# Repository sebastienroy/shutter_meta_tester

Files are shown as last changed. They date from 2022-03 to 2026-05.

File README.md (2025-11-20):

# shutter_meta_tester
A project which goal is to test the accuracy of shutter speed measurement tools.  

The general idea is to produce a well controlled shutter-like device.  
This device is used to produce a controlled open time, tested with a tool such as Shutter Speed Tester.  

If the measurement result of the tool is the same as the expected value, the measurement tool is accurate.  
The point is now to produce a well controlled open time. The target times are from 1s to 1/4000s.  

We consider two ways to simulate a shutter.  
1. The more theretical is to produce a "time slot" shutter. This kind of shutter consists in a source light that is lit during a controlled duration. This kind of shutter doesn't take into account the geometrical aspect of real shutter. However, it is a good mean to check the result (and its potential bias) due to the electronic circuit of the tester. The obtained results have to be taken with a "grain of salt" as the shutter testers usually come with their own light source.  
2. A simulated shutter more close to focal plane shutters (curtain shutters) consists in creating a slot that translates at a speed similar to real shutters. This can be achieved by creating a rotating wheel, with a well controlled rotation speed.

# Time Slot shutter

## Description

The faster shutter speed we want to measure is 1/4000s = 250 micro seconds.  
Because the response time of an LED is very fast (about 10 nano seconds), it is possible produce a very well controlled light pulse using a microcontroler that lights on and off an LED. The pulse duration precision is induced by the precision of the microcontroler that controls the LED.  

## Pros/cons

- The pros
  - Easy to build
  - Easy to control the pulse duration
  - Can differentiate a potential bias due to the electronic circuit from the bias due to geometrical consideration
- The cons
  - Does not take into account the physical phenomenos induced by a physical shutter.
  - In particular, the LED produces really sharp rising anf falling edges that are absolutely not representative of real worl shutters. Real world shutter have smooth egdges. For instance, the fastest leaf shutters take 1/200s to open and 1/200s to close. In case of focal plane shutters, even though the curtains are sharp, they are measured by a sensor wich is not a single point. In case of 3mm large sensor, the rizing edge is approximately 1/1000s and the same for the falling edge.
 
## Conclusion  
What maes the real world shutter difficult to measure is that the light signal has no sharp egdge, contrary to a LED that is simply switched on and off.  
So, **using an LED to test a shutter tester does not brings any information on the accuracy of the tester**. 

## Schema  

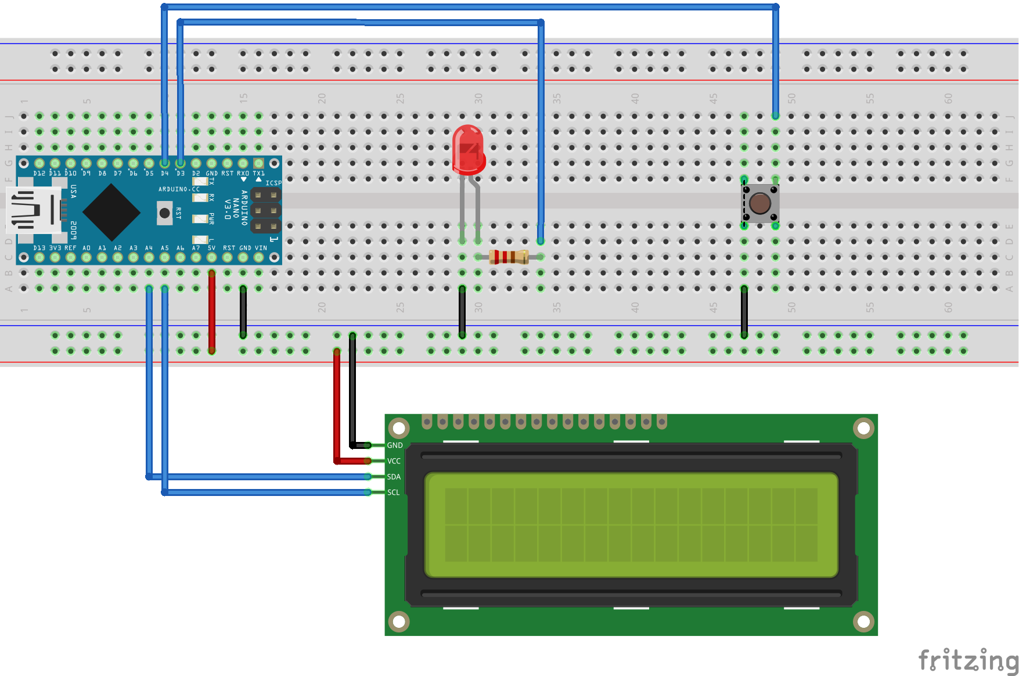
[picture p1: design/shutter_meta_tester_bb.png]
Tester schema


And the code is here :  
[Shutter Meta Tester Code](shutter_meta_tester/shutter_meta_tester.ino)

Usage :  
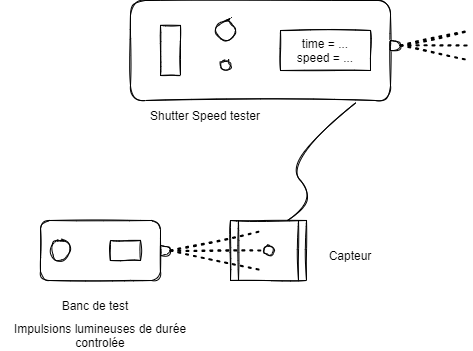
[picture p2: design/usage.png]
Usage


---

# Rotating wheel method
## Description
The idea is to use a wheel that rotates at a controlled frequency. By opening a slot in the wheel, we have the following open time :  

t = d / (2 x Pi x R x F)  

Where  
- t is the opened duration
- d is the size of the slot
- R is the radius from the wheel axis to the hole
- F is the wheel rotation frequency
 
## Pros/cons
- The pros
  - Very close to a real shutter
- The cons
  - A lot of hardware to buy
  - A lot of hardware to control 
  - A lot of parts to 3D print
 
## Conclusion
A **rotating wheel** is a lot more complicated to build than simple LED circuit, but it **is mandatory to be a little bit reprensentative of a real world shutter**.  
  
## Schema
We make the choice to control a wheel rotation using a stepper motor. The stepper motor has the advantage to be drivable very precisely, without any further regulation circuit. This stepper motor is controlled using an L298N board. This board is itself driven through the GPIO 14, 15, 16 and 17 of a Raspberry Pi Pico board.  
A push button, connected on GPIO 18, allows to start and stop the motor.  
The whole stuff is powered using a 12V DC adapter. The 5V output of the L298N bard is used to power the microcontroler board.  
The Rpi Pico has been chosen because it is cheap, available, efficient and fun : we can program it using MicroPython language (see [Rpi Pico MicroPython documentation](https://www.raspberrypi.com/documentation/microcontrollers/micropython.html))  
The microPython code used to drive all that is here. 

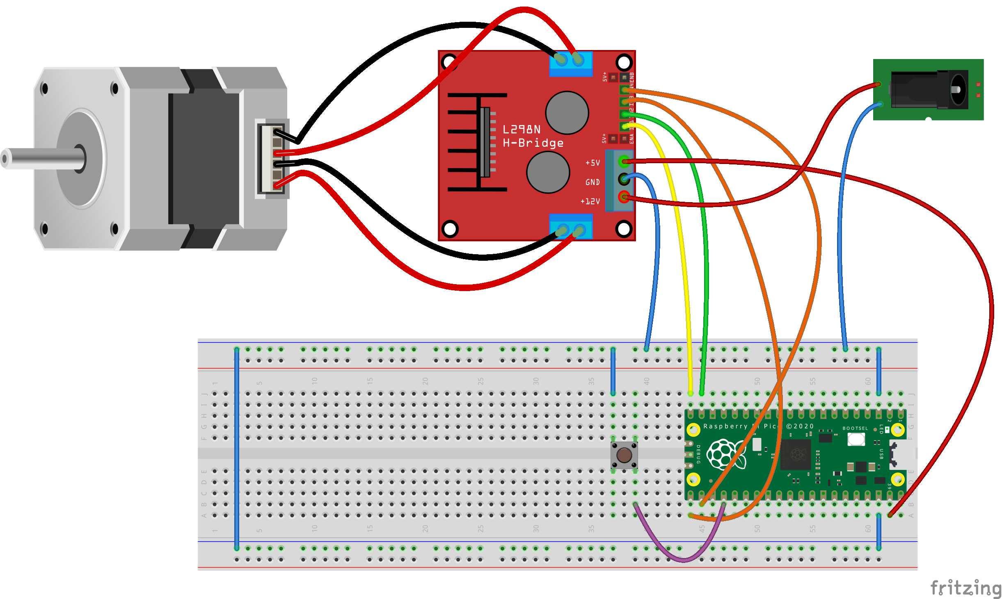
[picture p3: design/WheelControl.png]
Wheel control schema


### Bill Of Material (BOM)  

| Component | Reference|
|---|---|
| Microcontroler | https://www.kubii.fr/cartes-raspberry-pi/3205-raspberry-pi-pico-3272496311589.html#/477-version_pico-pico |
| Stepper motor | https://www.gotronic.fr/art-moteur-17hs15-0404s-18354.htm |
| Motor controller  | https://www.gotronic.fr/art-commande-de-2-moteurs-sbc-motodriver2-27418.htm |
| Power unit | 12V DC adapter (taken from a spare electronic equiment) |

## The Wheel

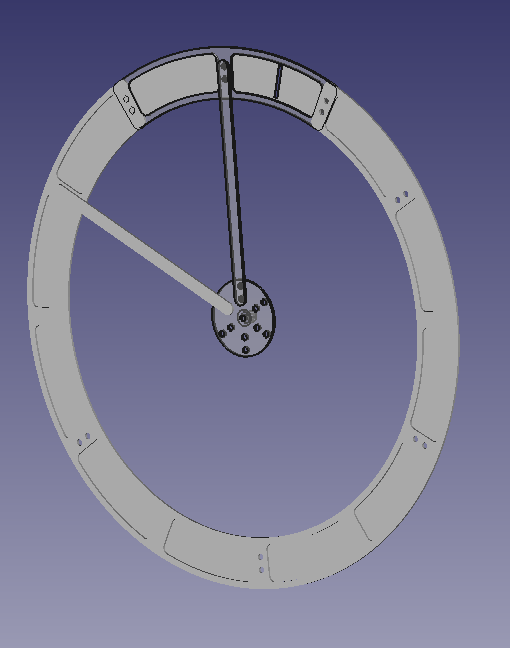
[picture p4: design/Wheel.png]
The wheel


We make the choice to use a 2.5rps rotation speed. This allows to have a well controlled speed. A strong torke at this speed ensures a great confidence on the speed accuracy.

We can see in the service manual of vintage cameras that curtain travel speed has to be set to about 3m/s (precisely to 14ms for 36mm translation) : [Pentax Spotmatic Service Manual](https://learncamerarepair.com/downloads/pdf/pentax-spotmatic-service.pdf)

So we will build our wheel to get a rotating window with the same value for its linear speed

This mean a wheel radius of : v = 2*pi*Rf  
- v=3000mm/s
- pi=atan(-1)
- R=radius
- f=2.5 s-1  

Conclusion : the wheel radius **R=191mm**

The [wheel](design/Wheel.png) is designed using FreeCad 0.20.2 and built using 3D printing.  
It has a central hub, 6 spokes and a rim made of 6 parts. Each part of the rim has 2 open windows.  
11 of the windows are completely masked. The last one has an opening in it that simulates the camera shutters.  
In order to simulate a shutter speed of 1/1000th of a second, the distance between the two sides of the window shall be 3mm.

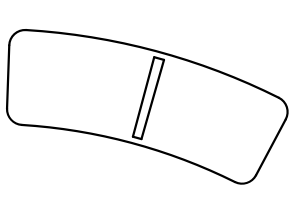
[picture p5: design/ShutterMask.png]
simulated shutter


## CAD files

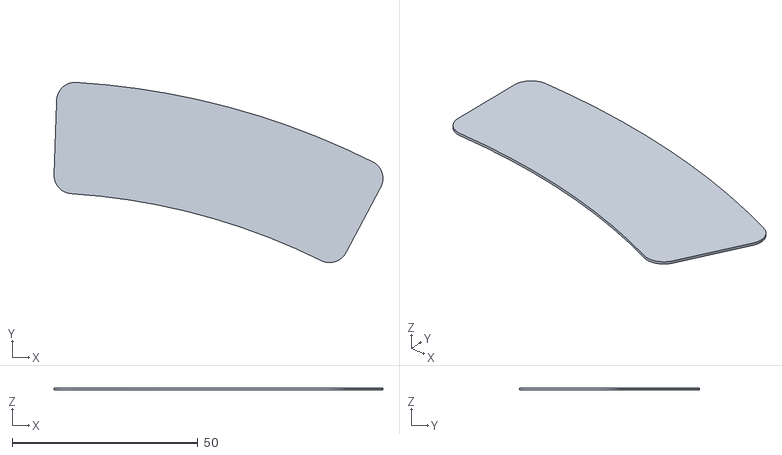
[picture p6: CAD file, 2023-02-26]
wheel/parts/wheel-mask.stl
88.6 x 48.5 x 0.6

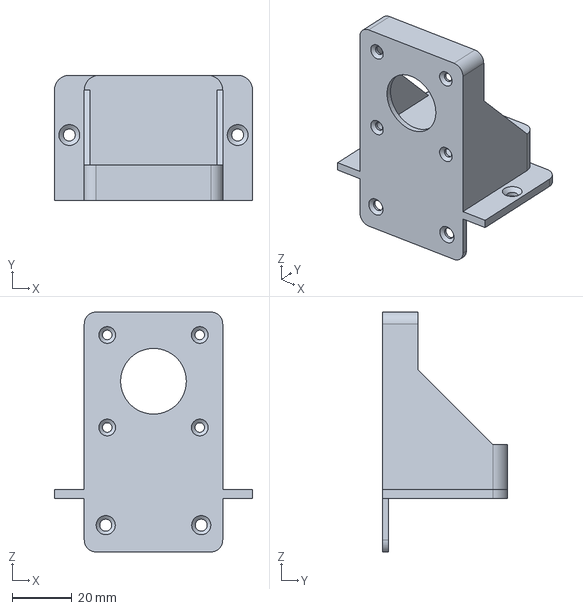
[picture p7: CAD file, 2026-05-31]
wheel/SupportStepMotor.FCStd
66.4 x 42.0 x 80.4 mm

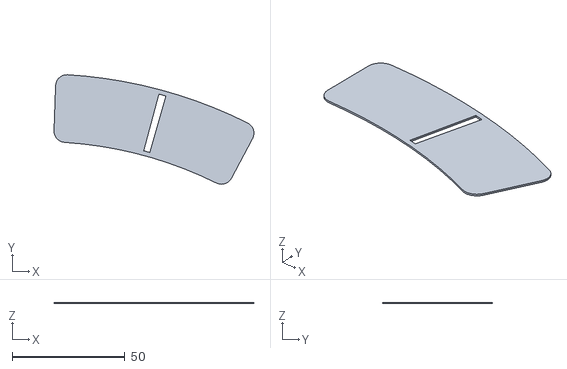
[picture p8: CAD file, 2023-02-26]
wheel/parts/wheel-mask_3mm.stl
88.6 x 48.5 x 0.6

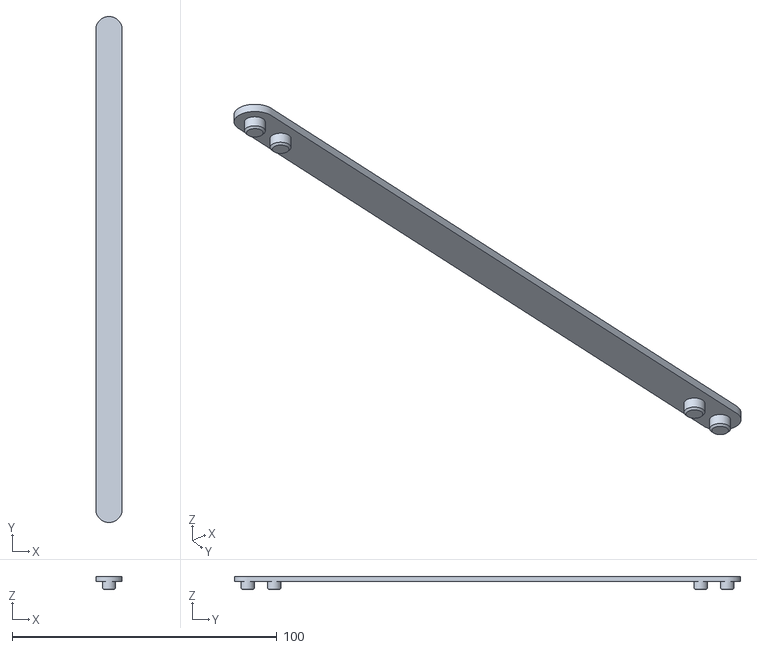
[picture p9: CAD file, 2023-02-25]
wheel/parts/wheel-spoke.stl
10.0 x 191.0 x 5.00

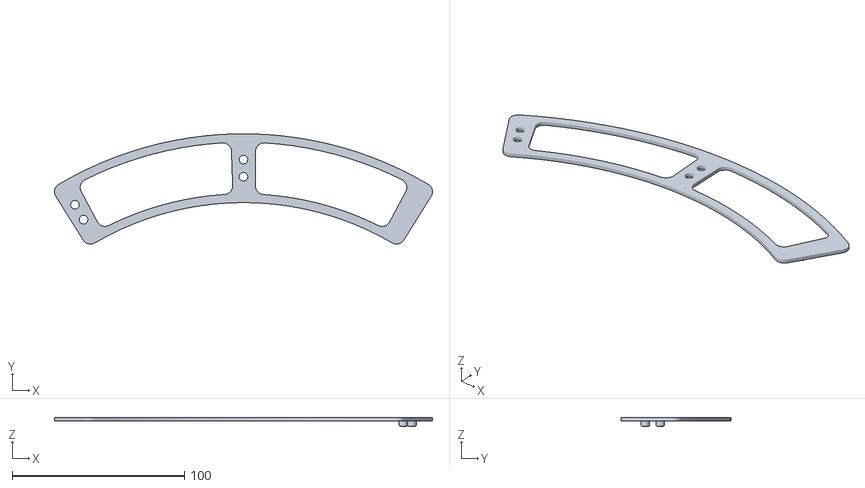
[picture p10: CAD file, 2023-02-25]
wheel/parts/wheel-rim.stl
219.8 x 64.1 x 5.00

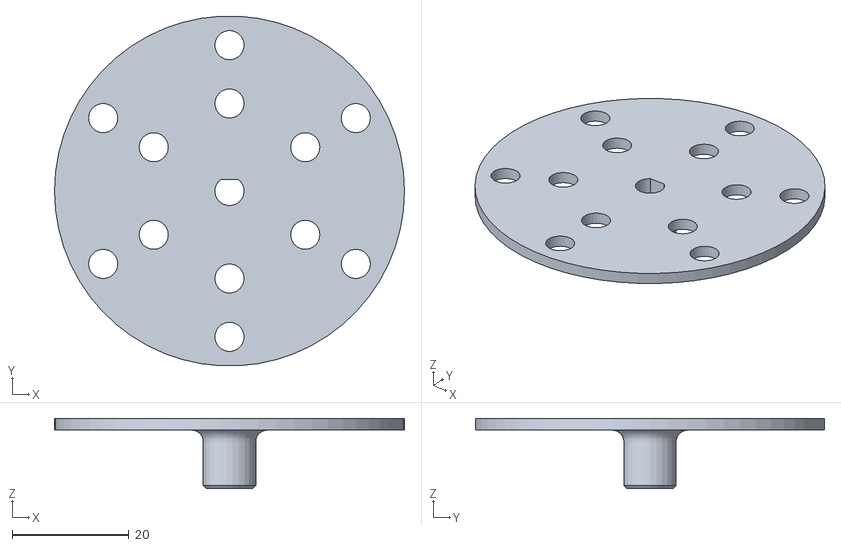
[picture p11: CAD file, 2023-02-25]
wheel/parts/wheel-hub.stl
60.0 x 59.9 x 12.0

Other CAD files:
wheel/wheel.FCStd

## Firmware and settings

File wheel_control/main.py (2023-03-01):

from machine import Pin, Timer, I2C
#from ssd1306 import SSD1306_I2C
import utime

stepTimer = Timer()
accelerationTimer = Timer()

buttonPin = 18
buttonState = 1

currentSpeed = 0
maxSpeed = 500

accelerationFreq = 10
accelerationStep = 5

accelerationValue = 1

#i2c = I2C(0, scl=Pin(21), sda=Pin(20), freq=400000)
#oled = SSD1306_I2C(128, 64, i2c)

#oled.fill(0)
#oled.text("Pico",5,15)
#oled.show()

current_step = 0

motorPins = [
             Pin(14, Pin.OUT),  # A+
             Pin(15, Pin.OUT),  # A-
             Pin(17, Pin.OUT),   # B- 
             Pin(16, Pin.OUT)  # B+
             ]
led = Pin(25, Pin.OUT)

full_step_seq = [ 
            [1,0,1,0], # AB 
            [0,1,1,0], # A/B 
            [0,1,0,1], # A/B/
            [1,0,0,1]] # AB/
single_step_seq = [ 
            [1,0,0,0], # A 
            [0,0,1,0], # B 
            [0,1,0,0], # A/
            [0,0,0,1]] # B/

button = Pin(buttonPin, mode=Pin.IN, pull=Pin.PULL_UP)

# begin
led.value(1)

def step(timer):
    global current_step
    for pin in range(4):
        motorPins[pin].value(single_step_seq[current_step][pin])
    current_step = (current_step + 1) % 4
    
def accelerate(timer):
    global currentSpeed, accelerationValue, accelerationStep
    currentSpeed = currentSpeed + accelerationValue * accelerationStep
    if(currentSpeed <= 0):
        currentSpeed = 0
        accelerationValue = 0
        accelerationTimer.deinit()
        stepTimer.deinit()
        for pin in range(4):
            motorPins[pin].value(0)
    elif(currentSpeed >= maxSpeed):
        currentSpeed = maxSpeed
        accelerationValue = 0
        accelerationTimer.deinit()
        
    if(currentSpeed != 0):
        stepTimer.init(freq=currentSpeed, mode=Timer.PERIODIC, callback=step)
    
def setAcceleration(value):
     global accelerationValue
     accelerationValue = value
     accelerationTimer.init(freq=accelerationFreq, mode=Timer.PERIODIC, callback=accelerate)       


def checkButton():
    global buttonState, accelerationValue, currentSpeed
    currentState = button.value()
    
    if(currentState == 0 and currentState != buttonState):
        if(currentSpeed == 0):
            setAcceleration(1)
        elif(currentSpeed == maxSpeed):
            setAcceleration(-1)
        else:
            setAcceleration(accelerationValue*-1)
    
    buttonState = currentState
    
def checkTest():
    val=button.value()
    led.value(val)
    utime.sleep(1)

led.value(1)

while(True):
    checkButton()
    utime.sleep_ms(100)
#end
led.value(0)

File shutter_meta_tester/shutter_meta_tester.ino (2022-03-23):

const byte LED_PIN = 3;
const byte BUTTON_PIN = 4;

// pulses duration, in microseconds
//                1/1000   1/2000  1/4000  1/8000
int pulses[] = {   1000,     500,     250,   125};
int pulses_nb = 4;
int pulse_index = 0;
// nb of pulse of each value
int repeat_nb = 3;
int repeat_index = 0;

int previous_duration = -1;

// default is up (1)
byte previous_button_state = 1;


void setup() {

  Serial.begin(9600);

  pinMode(LED_PIN, OUTPUT);
  pinMode(BUTTON_PIN, INPUT_PULLUP);

  Serial.print("Next pulse duration (microseconds) : ");
  Serial.println(pulses[pulse_index]);

}

void loop() {
  // put your main code here, to run repeatedly:
  byte current_button_state = digitalRead(BUTTON_PIN);
  if(current_button_state == LOW && current_button_state != previous_button_state) {
      digitalWrite(LED_PIN, HIGH);
      delayMicroseconds(pulses[pulse_index]);
      digitalWrite(LED_PIN, LOW);

      repeat_index++;
      if(repeat_index >= repeat_nb) {
        repeat_index = 0;
        pulse_index++;
        if(pulse_index >= pulses_nb) {
          pulse_index = 0;
        }
      }
      Serial.print("Next pulse duration (microseconds) : ");
      Serial.println(pulses[pulse_index]);
    
    
  }
  previous_button_state = current_button_state;
  delay(100);


}

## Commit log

2022-02-23 Introduce LED method
2022-03-18 design of the benchmark tool
    [shutter_meta_tester.fzz]
2022-03-23 First version of arduino code
2022-03-26 add sketch
    [shutter_meta_tester.fzz]
2023-02-25 Add fritzing schema for wheel control
    [WheelControl.fzz]
2023-02-25 add wheel model
    [wheel-hub.stl, wheel-mask.stl, wheel-mask_3mm.stl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]
2023-02-25 add wheel picture
2023-02-26 updates on model
    [wheel-mask.stl, wheel-mask_3mm.stl, wheel.FCStd]
2023-02-26 add button
2023-02-28 update schema
    [WheelControl.fzz]
